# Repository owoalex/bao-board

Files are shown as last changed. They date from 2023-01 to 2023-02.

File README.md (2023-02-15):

# bao-board
Experimental BLDC driver board based on the RP2040.
Compatible with the open source [v3fkontroller](https://github.com/owoalex/v3fkontroller) firmware.

## BOM for v1.3
| Part | Mfr Part No | #  | GBP | Total | Refs |
| --- | --- | -- | ----- | ----- | --- |
| RS PRO 10μF Axial Electrolytic Capacitor 35V | 707-6391 |  3 |  0.26 |  0.78 | C1-3 |
| Murata 1μF Multilayer Ceramic Capacitor 1uF 50V | RCER71H105K2K1H03B |  3 |  0.56 |  1.67 | C4-6 |
| 100pF 1206 SMD Capacitors | GENERIC |  2 |  0.05 |  0.10 | C7-8 |
| RS PRO 100μF Axial Electrolytic Capacitor 100V | 707-6552 |  1 |  1.01 |  1.01 | C9 |
| RS PRO 1000μF Axial Electrolytic Capacitor 25V | 707-6650 |  1 |  0.92 |  0.92 | C10 |
| STTH2R06 Rectifier (PN) Diode 600V 2A | STTH2R06 |  3 |  0.55 |  1.66 | D1-3 |
| STM 150V 3A Schottky Diode DO-201AD | STPS3150RL |  1 |  0.37 |  0.37 | D4 |
| Kingbright 2.2 V Green LED 3216 (1206) SMD | KP-3216SGC |  2 |  0.18 |  0.36 | D5-6 |
| ASSMANN Socket Type B 2.0 USB Connector | A-USBSB |  1 |  1.29 |  1.29 | J1 |
| RS PRO 100uH 3A IDC Inductor | 104-8436 |  1 |  0.99 |  0.99 | L1 |
| Infineon 75V 80A N-Channel MOSFET (TO-220) | IRFB3607PBF | 12 |  1.07 | 12.84 | Q1-12 |
| TE Connectivity 1kΩ Carbon Film Resistor 0.33W | CFR25J1K0 |  6 |  0.12 |  0.74 | R1-6 |
| 33Ω 1206 SMD Resistors | GENERIC |  2 |  0.05 |  0.10 | R7-8 |
| 100Ω 1206 SMD Resistors | GENERIC |  4 |  0.05 |  0.20 | R9-12 |
| 1kΩ 1206 SMD Resistors | GENERIC |  2 |  0.05 |  0.10 | R13-14  |
| Red Button Tactile Switch SPST | 479-1429 |  1 |  0.13 |  0.13 | SW1 |
| Infineon 20V MOSFET/IGBT Driver 28-Pin PDIP | IR2130PBF |  1 | 12.45 | 12.45 | U1 |
| Winslow 28-Way IC Dip Socket 0.6in Pitch | W3128TRC |  1 |  0.17 |  0.17 | (U1) |
| Raspberry Pi RP2040 | RP2040 |  1 |  0.85 |  0.85 | U2 |
| DiodesZetex 3.3V 1A Linear Regulator (SOT-223) | AZ1117H-3.3TRE1 |  1 |  0.10 |  0.10 | U3 |
| TI Buck Converter 12V 3A (5-Pin TO-220) | LM2576HVT-12 |  1 |  7.82 |  7.82 | U4 |
| Winbond 16Mb SPI Flash | W25Q16JVSNIQ |  1 |  0.67 |  0.67 | U5 |
| STM 5V 1A Pos LDO Regulator (TO-220) | L7805ACV |  1 |  0.76 |  0.76 | U6 |
| QANTEK 12MHz Crystal (HC-49/U-S) | QCL12.0000F18B23B  |  1 |  0.16 |  0.16 | Y1 |

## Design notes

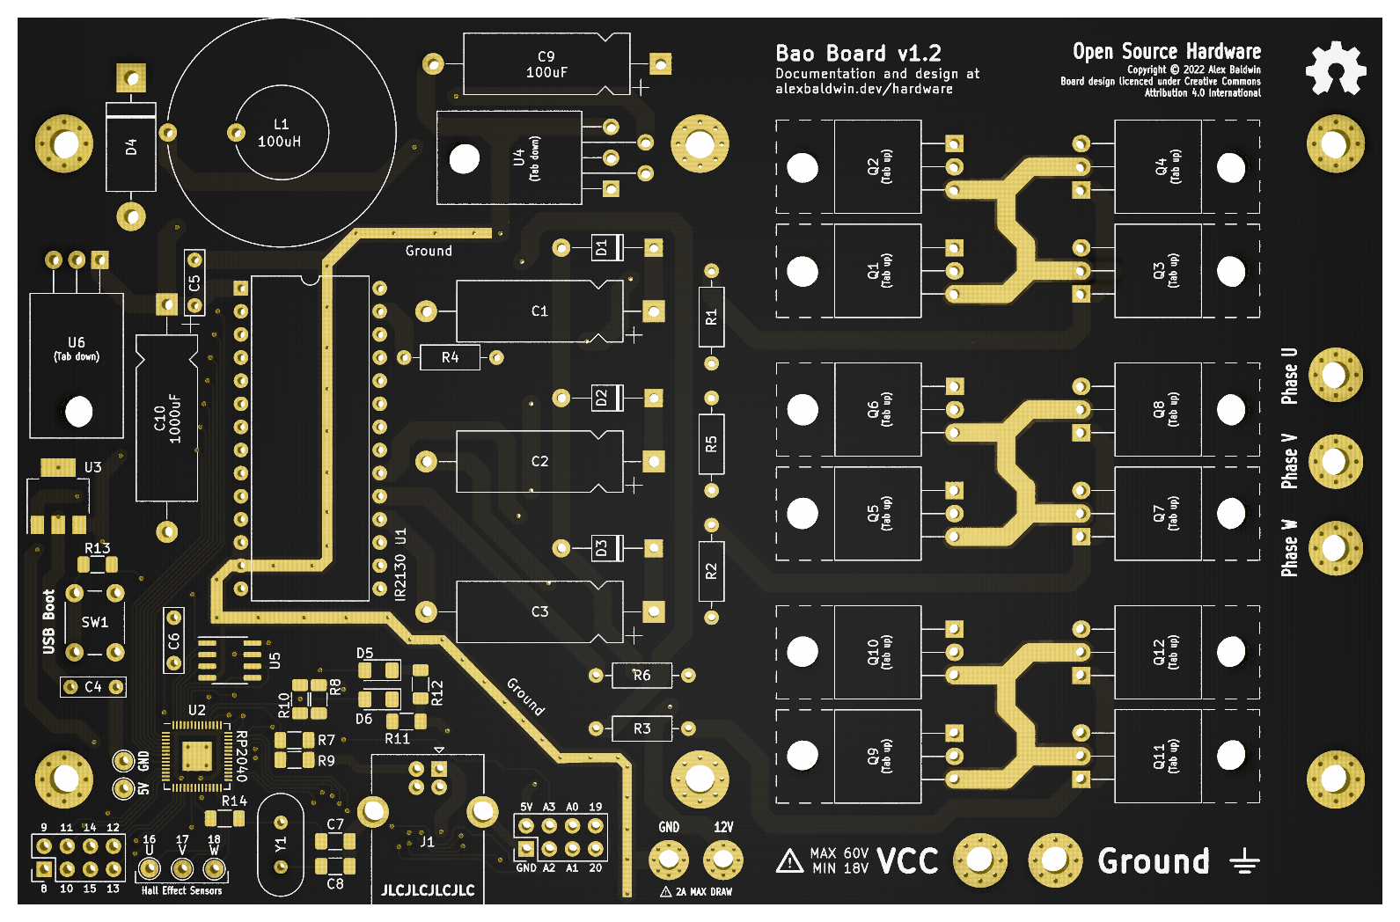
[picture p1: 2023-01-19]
bao-board.png

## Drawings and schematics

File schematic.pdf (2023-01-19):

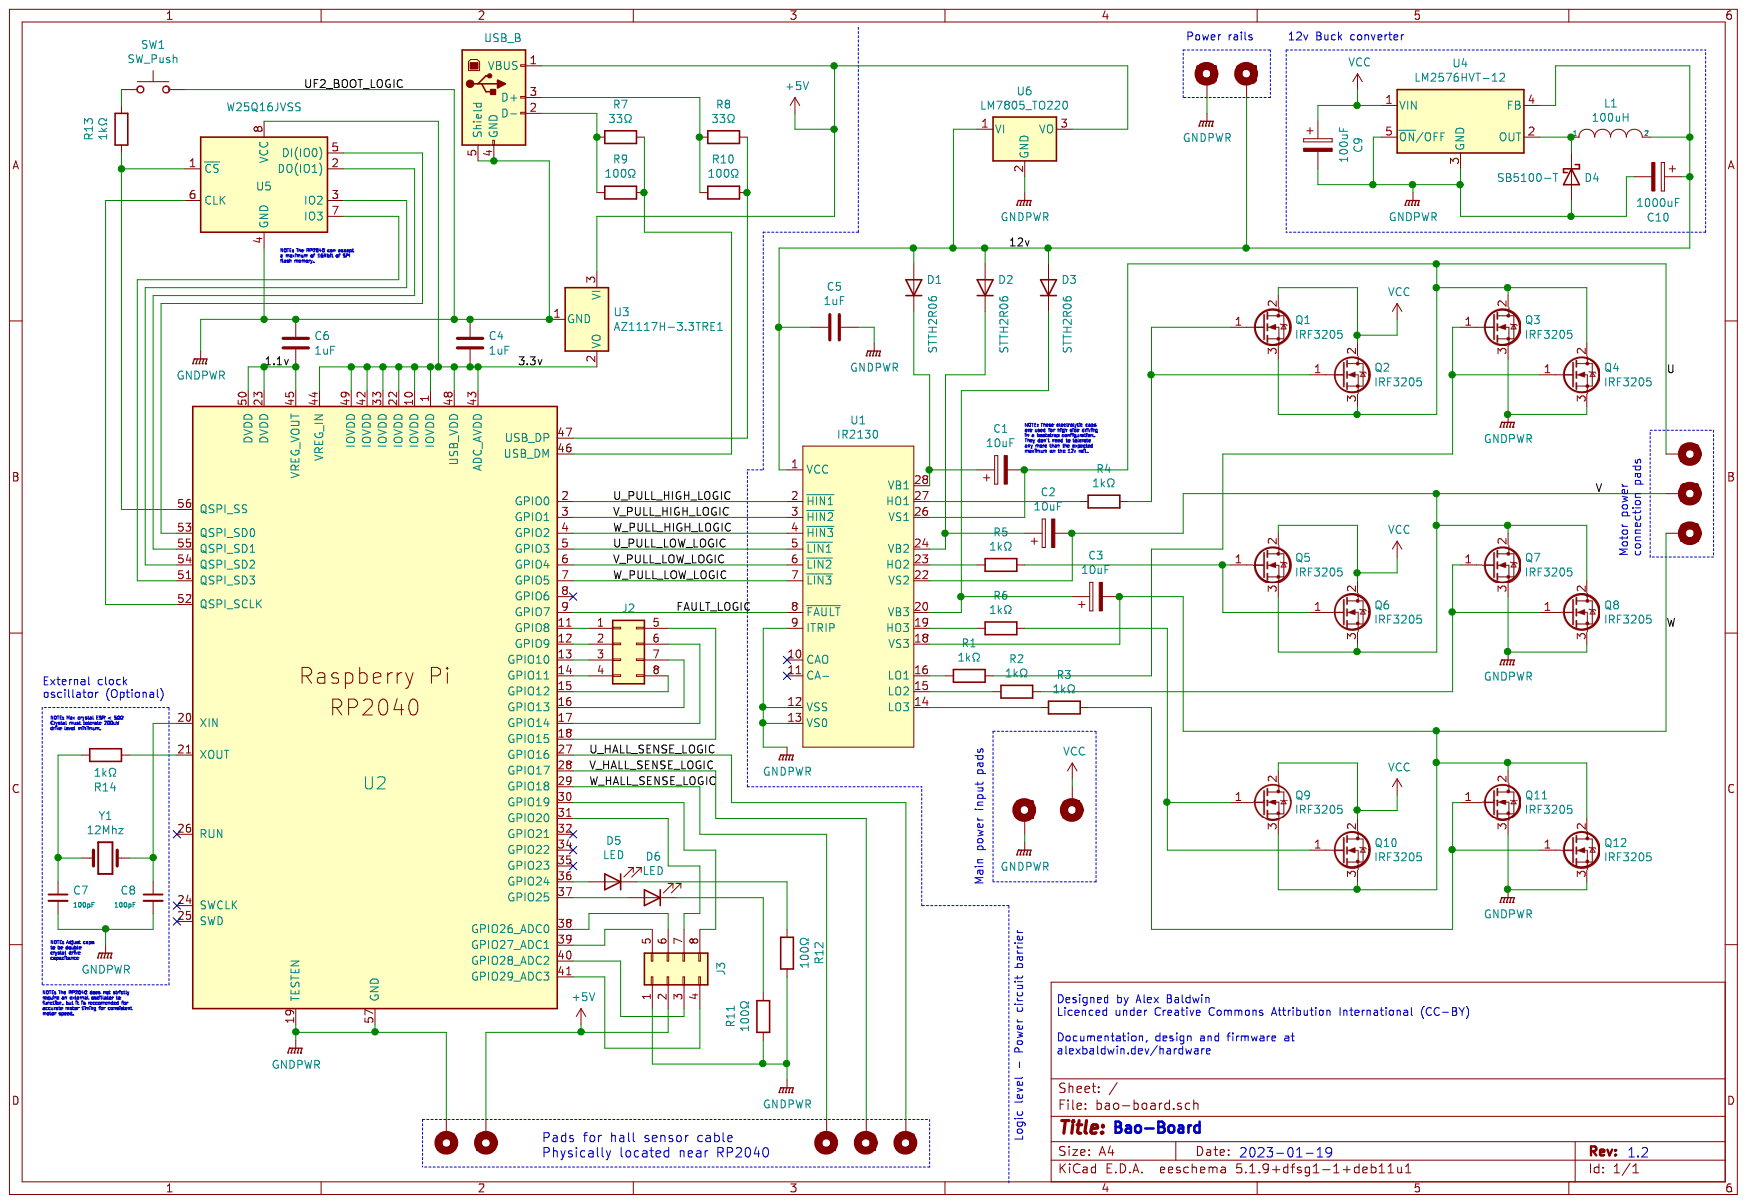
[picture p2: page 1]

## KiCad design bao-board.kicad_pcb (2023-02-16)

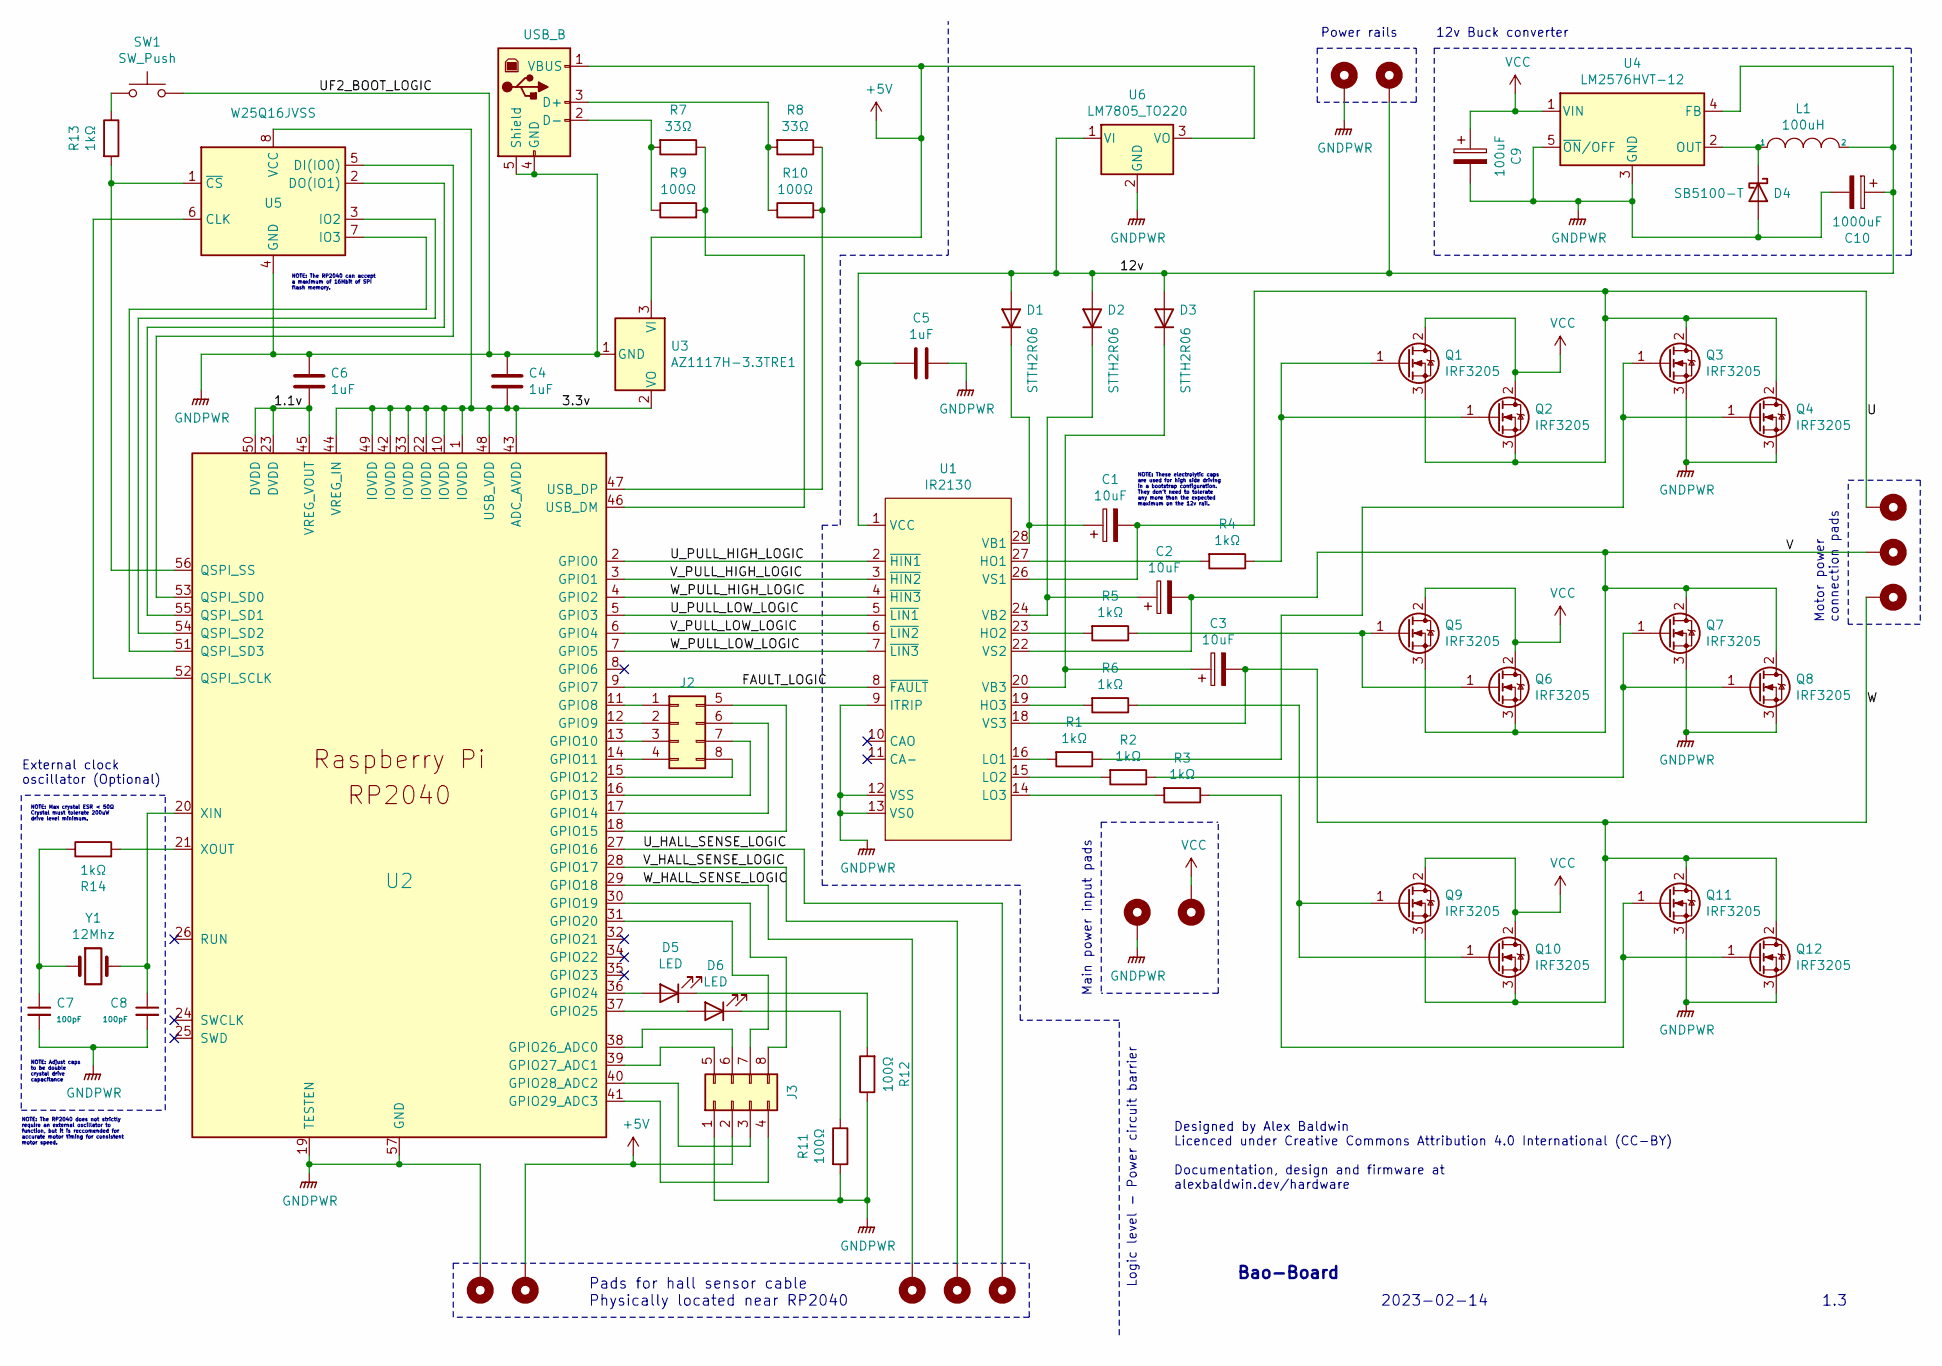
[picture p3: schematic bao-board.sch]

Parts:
C1, C2, C3: 10uF; CP_Axial_L18.0mm_D6.5mm_P25.00mm_Horizontal
C4, C5, C6: 1uF; C_Rect_L7.0mm_W2.0mm_P5.00mm
C7, C8: 100pF; C_1206_3216Metric_Pad1.33x1.80mm_HandSolder
C9: 100uF; CP_Axial_L18.0mm_D6.5mm_P25.00mm_Horizontal
C10: 1000uF; CP_Axial_L25.0mm_D10.0mm_P30.00mm_Horizontal
D1, D2, D3: STTH2R06; D_T-1_P10.16mm_Horizontal
D4: SB5100-T; D_DO-201AD_P15.24mm_Horizontal
D5, D6: LED; LED_1206_3216Metric_Pad1.42x1.75mm_HandSolder
H1, H2, H3, H4, H5: MountingHole_Pad; MountingHole_3mm_Pad_Via
H6, H7, H8, H9, H10: MountingHole_Pad; TestPoint_THTPad_D2.0mm_Drill1.0mm
H11, H13: MountingHole_Pad; MountingHole_2.2mm_M2_Pad_Via
J1: USB_B; USB_B_OST_USB-B1HSxx_Horizontal
J2, J3: Conn_02x04_Top_Bottom; PinHeader_2x04_P2.54mm_Vertical
L1: 100uH; THT Toroidal Inductor Horizontal 25x12mm
Q1, Q2, Q3, Q4, Q5, Q6, Q7, Q8, Q9, Q10, Q11, Q12: IRF3205; TO-220-3_Horizontal_TabUp
R1, R2, R3, R4, R5, R6: 1kΩ; R_Axial_DIN0207_L6.3mm_D2.5mm_P10.16mm_Horizontal
R7, R8: 33Ω; R_1206_3216Metric_Pad1.30x1.75mm_HandSolder
R9, R10, R11, R12: 100Ω; R_1206_3216Metric_Pad1.30x1.75mm_HandSolder
R13, R14: 1kΩ; R_1206_3216Metric_Pad1.30x1.75mm_HandSolder
SW1: SW_Push; SW_PUSH_6mm
U1: IR2130; DIP-28_W15.24mm
U2: RP2040
U3: AZ1117H-3.3TRE1; SOT-223-3_TabPin2
U4: LM2576HVT-12; TO-220-5_P3.4x3.8mm_StaggerEven_Lead7.13mm_TabDown
U5: W25Q16JVSS; SOIC-8_3.9x4.9mm_P1.27mm
U6: LM7805_TO220; TO-220-3_Horizontal_TabDown
Y1: 12Mhz; Crystal_HC49-U_Vertical

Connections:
+5V: H9.1, J1.1 (VBUS), J3.2, U3.3 (VI), U6.3 (VO)
/1.1v: C6.2, U2.23 (DVDD), U2.45 (VREG_VOUT), U2.50 (DVDD)
/3.3v: C4.2, U2.1 (IOVDD), U2.10 (IOVDD), U2.22 (IOVDD), U2.33 (IOVDD), U2.42 (IOVDD), U2.43 (ADC_AVDD), U2.44 (VREG_IN), U2.48 (USB_VDD), U2.49 (IOVDD), U3.2 (VO), U5.8 (VCC)
/12v: C5.1, C10.1, D1.2 (A), D2.2 (A), D3.2 (A), H13.1, L1.2, U1.1 (VCC), U4.4 (FB), U6.1 (VI)
/FAULT_LOGIC: U1.8 (~FAULT), U2.9 (GPIO7)
/U: C1.2, H1.1, Q1.3 (S), Q2.3 (S), Q3.2 (D), Q4.2 (D), U1.26 (VS1)
/U_HALL_SENSE_LOGIC: H6.1, U2.27 (GPIO16)
/U_PULL_HIGH_LOGIC: U1.2 (~HIN1), U2.2 (GPIO0)
/U_PULL_LOW_LOGIC: U1.5 (~LIN1), U2.5 (GPIO3)
/V: C2.2, H2.1, Q5.3 (S), Q6.3 (S), Q7.2 (D), Q8.2 (D), U1.22 (VS2)
/V_HALL_SENSE_LOGIC: H7.1, U2.28 (GPIO17)
/V_PULL_HIGH_LOGIC: U1.3 (~HIN2), U2.3 (GPIO1)
/V_PULL_LOW_LOGIC: U1.6 (~LIN2), U2.6 (GPIO4)
/W: C3.2, H3.1, Q9.3 (S), Q10.3 (S), Q11.2 (D), Q12.2 (D), U1.18 (VS3)
/W_HALL_SENSE_LOGIC: H8.1, U2.29 (GPIO18)
/W_PULL_HIGH_LOGIC: U1.4 (~HIN3), U2.4 (GPIO2)
/W_PULL_LOW_LOGIC: U1.7 (~LIN3), U2.7 (GPIO5)
GNDPWR: C4.1, C5.2, C6.1, C7.2, C8.2, C9.2, C10.2, D4.2 (A), H5.1, H10.1, H11.1, J1.4 (GND), J1.5 (Shield), J3.1, Q3.3 (S), Q4.3 (S), Q7.3 (S), Q8.3 (S), Q11.3 (S), Q12.3 (S), R11.2, R12.1, SW1.2, U1.9 (ITRIP), U1.12 (VSS), U1.13 (VS0), U2.19 (TESTEN), U2.57 (GND), U3.1 (GND), U4.3 (GND), U4.5 (~ON~/OFF), U5.4 (GND), U6.2 (GND)
unnamed: C1.1, D1.1 (K), U1.28 (VB1)
unnamed: C2.1, D2.1 (K), U1.24 (VB2)
unnamed: C3.1, D3.1 (K), U1.20 (VB3)
unnamed: C7.1, R14.1, Y1.1
unnamed: C8.1, U2.20 (XIN), Y1.2
unnamed: D4.1 (K), L1.1, U4.2 (OUT)
unnamed: D5.1 (K), R12.2
unnamed: D5.2 (A), U2.36 (GPIO24)
unnamed: D6.1 (K), R11.1
unnamed: D6.2 (A), U2.37 (GPIO25)
unnamed: J1.2 (D-), R7.2, R9.1
unnamed: J1.3 (D+), R8.2, R10.1
unnamed: J2.1, U2.11 (GPIO8)
unnamed: J2.2, U2.12 (GPIO9)
unnamed: J2.3, U2.13 (GPIO10)
unnamed: J2.4, U2.14 (GPIO11)
unnamed: J2.5, U2.18 (GPIO15)
unnamed: J2.6, U2.17 (GPIO14)
unnamed: J2.7, U2.16 (GPIO13)
unnamed: J2.8, U2.15 (GPIO12)
unnamed: J3.3, U2.40 (GPIO28_ADC2)
unnamed: J3.4, U2.41 (GPIO29_ADC3)
unnamed: J3.5, U2.39 (GPIO27_ADC1)
unnamed: J3.6, U2.38 (GPIO26_ADC0)
unnamed: J3.7, U2.31 (GPIO20)
unnamed: J3.8, U2.30 (GPIO19)
unnamed: Q1.1 (G), Q2.1 (G), R4.1
unnamed: Q3.1 (G), Q4.1 (G), R1.1
unnamed: Q5.1 (G), Q6.1 (G), R5.1
unnamed: Q7.1 (G), Q8.1 (G), R2.1
unnamed: Q9.1 (G), Q10.1 (G), R6.1
unnamed: Q11.1 (G), Q12.1 (G), R3.1
unnamed: R1.2, U1.16 (LO1)
unnamed: R2.2, U1.15 (LO2)
unnamed: R3.2, U1.14 (LO3)
unnamed: R4.2, U1.27 (HO1)
unnamed: R5.2, U1.23 (HO2)
unnamed: R6.2, U1.19 (HO3)
unnamed: R7.1, R9.2, U2.46 (USB_DM)
unnamed: R8.1, R10.2, U2.47 (USB_DP)
unnamed: R13.1, SW1.1
unnamed: R13.2, U2.56 (QSPI_SS), U5.1 (~CS)
unnamed: R14.2, U2.21 (XOUT)
unnamed: U2.51 (QSPI_SD3), U5.7 (IO3)
unnamed: U2.52 (QSPI_SCLK), U5.6 (CLK)
unnamed: U2.53 (QSPI_SD0), U5.5 (DI(IO0))
unnamed: U2.54 (QSPI_SD2), U5.3 (IO2)
unnamed: U2.55 (QSPI_SD1), U5.2 (DO(IO1))
VCC: C9.1, H4.1, Q1.2 (D), Q2.2 (D), Q5.2 (D), Q6.2 (D), Q9.2 (D), Q10.2 (D), U4.1 (VIN)

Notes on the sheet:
Designed by Alex Baldwin Licenced under Creative Commons Attribution 4.0 International (CC-BY) Documentation, design and firmware at alexbaldwin.dev/hardware
Bao-Board
1.3
2023-02-14
NOTE: Max crystal ESR < 50Ω Crystal must tolerate 200uW drive level minimum.
NOTE: Adjust caps to be double crystal drive capacitance
Pads for hall sensor cable Physically located near RP2040
Main power input pads
Motor power connection pads
Logic level - Power circuit barrier
12v Buck converter
NOTE: The RP2040 can accept a maximum of 16Mbit of SPI flash memory.
NOTE: These electrolytic caps are used for high side driving in a bootstrap configuration. They don't need to tolerate any more than the expected maximum on the 12v rail.
NOTE: The RP2040 does not strictly require an external oscillator to function, but it is reccomended for accurate motor timing for consistent motor speed.
External clock oscillator (Optional)
Power rails

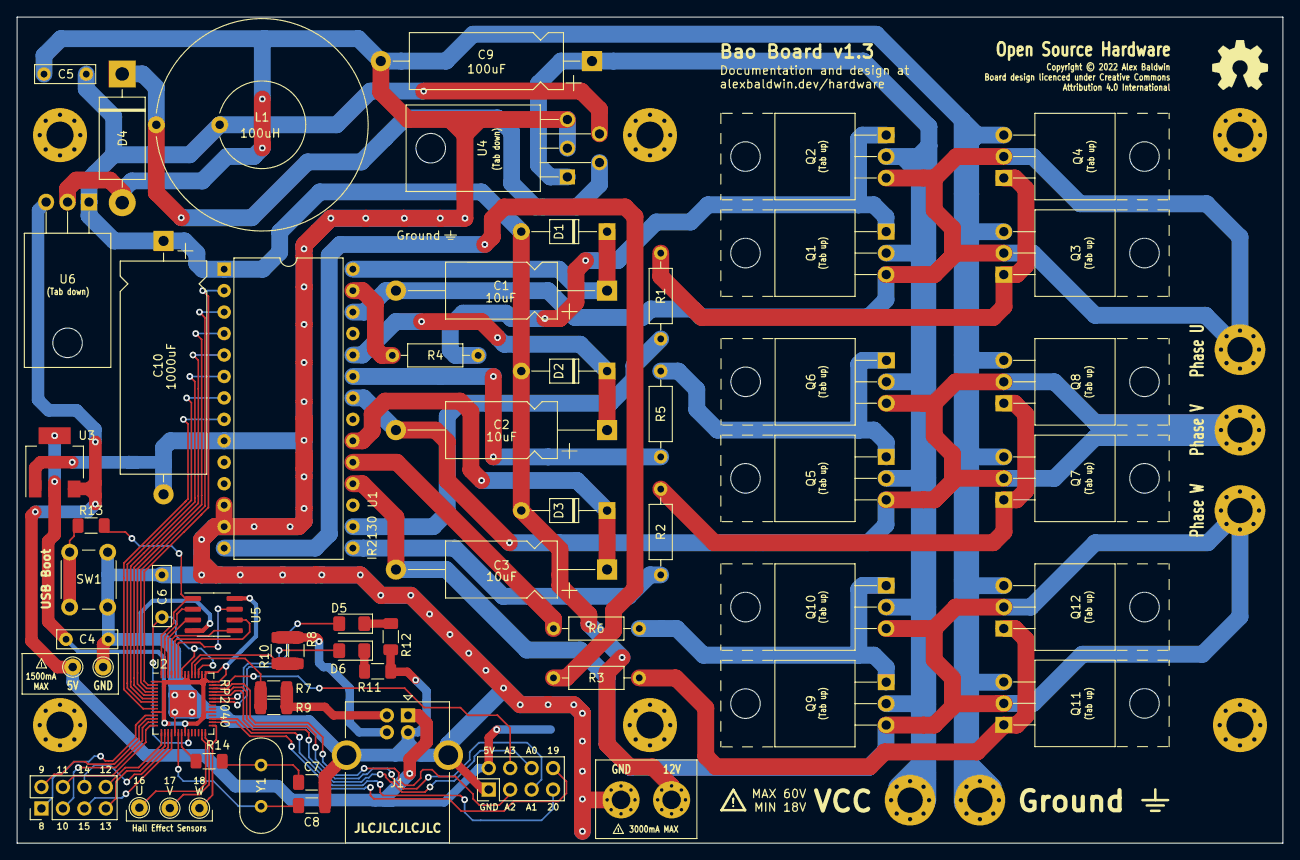
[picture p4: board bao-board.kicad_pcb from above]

Board: 2 copper layers, 149.9 x 97.8 mm, 66 parts (0 on the bottom side), 67 nets.

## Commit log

2023-01-18 Initial work
    [bao-board.kicad_pcb, bao-board.sch]
2023-01-19 Updated to expose analog inputs instead of using for motor hall. Refined track routing
    [bao-board.kicad_pcb, bao-board.sch]
2023-02-15 Design refinement for v1.3
    [bao-board.kicad_pcb, bao-board.sch]
2023-02-16 Slightly revised design, version sent of to fab
    [bao-board-B_Cu.gbr, bao-board-B_Mask.gbr, bao-board-Edge_Cuts.gbr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]

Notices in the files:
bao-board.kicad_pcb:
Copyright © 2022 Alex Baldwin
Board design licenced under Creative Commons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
